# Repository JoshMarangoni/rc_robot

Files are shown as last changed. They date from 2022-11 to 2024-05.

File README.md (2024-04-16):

# rc_robot

## Project Motivation

NASA's Perseverance rover is a remote controllable rover designed to explore the surface of the Red Planet. The rover primarily uses an ultra-high frequency antenna to communicate with Earth. Data is relayed through Mars satellites back to Earth where engineers can monitor the robot's trajectory and speed.

Although my robot is not designed for Mars, it is designed to explore the outer reaches of my kitchen and living room while I am comfortably relaxing in my bedroom. Instead of orbitting satellites I use my WiFi network and communicate with my robot using http requests. This project is intended to emulate a remote controlled rover such as Perserverence, using my own circuit and software designs.

## Requirements

- Must be able to drive in any direction
- Programmed in C/C+
- Non-arduino based coding envrionment
- Battery powered
- Map "WASD" keys to driving direction

## Bonus features

- All electronics contained on one PCB
- Remote controlled using video feed
- Lag between key presses and robot response < 0.5 s

## Design 1 (MVP) - DONE

- ESP 32 microcontroller programmed in Arduino
- 2 wheels/motors in the rear (RWD)
- 1 wheel/motor in the front
- esp32CAM for video streaming
- Plexiglass chassis

## Design 2 (Feature Complete) - Done

- ESP32 programmed in Expressif IoT Development Framework
- PCB designed in KiCAD and fabricated by JLC PCB
- control terminal for WASD keys written in Python

### Planning (created after completing Design 1)
| Task | Deadline |
|---|---|
| get 3D printer working | Nov.19 (Sat) |
| receive MOSFETs | Nov.19 (Sat) |
| get H-bridges working | Nov.20 (Sun) |
| test singular power source with capacitor | Nov.20 (Sun) |
| finish PCB design and send order for fab | Nov.27 (Sun) |
| make CAD drawing for chassis and 3D print | Dec.4  (Sun) |
| receive PCB | Dec.7  (Wed) |
| solder components on PCB and test | Dec.11 (Sun) |
| finish all software | Dec.18 (Sun) |

### Demo YouTube Videos
H bridge Circuit Theory - 2 Wire Input Design (https://www.youtube.com/watch?v=d1yoUQiy7Vs)

Making an H Bridge PCB in KiCad from scratch! (https://www.youtube.com/watch?v=Di--UKmRp28)

Assembling and Testing ESP32 H Bridge PCB (https://www.youtube.com/watch?v=TdYsxLpm71Q)

Remote Control Robot with ChatGPT and Embedded Web Server on ESP32 (https://www.youtube.com/watch?v=ufaAewCI-w4)

### Key Learnings
- even though a motor draws 0.2 A while running it can produce a stall current of 2+ A, causing the driver to underpower the arduino
  - meaured the 5V output of the Arduino and saw the voltage hang around 3 V sometimes dropping even lower as the motors change directions. I need to either put the motors on a separate power supply or use large capacitors to buffer voltage spikes
  - After doing some research I found out that the larger the current draw is from the battery, the lower the batteries output voltage will be due to the internal voltage drop. Batteries have an internal resistance, so the larger the current out of the battery, the larger the internal drop, and the lower the output voltage will be. Hypothesis, to solve this, use batteries with larger capacity, such as two 18650's in series, which have a combined 2800mAh capacity. Results: it worked!
- Got video streaming over Bluetooth by changing ArduCAM's serial prints to use SerialBT, then using a BT virtual COM port for the host app
- Tried combining all the camera source code, bluetooth serial, http webserver, and motor controls all in one program, but the program is too large for the ESP32. Further, I do not want the camera streaming software to be delayed by running motor controls and http server responses in the same control loop. I could use FreeRTOS to split up these tasks, but that seems overkill. There is no need to have all this code on one processor when I can buy an integrated esp32-CAM that I can dedicate to video streaming. Having the robot be controlled over WIFI is also superior to Bluetooth as it allows me to operate the vehicle compleletely remotely as long as I have the WIFI router's IP address and port forwarding setup.
- Do a beep test on a PCB before placing components
- DO NOT POWER UP PCB UNTIL YOU ARE SURE EVERYTHING IS CONNECTED PROPERLY
- BE VERY SURE you don't mix up power and ground, as reversing the polarity will surely fry your components
- If hand soldering a PCB, do it in stages, and test each module individually as you go

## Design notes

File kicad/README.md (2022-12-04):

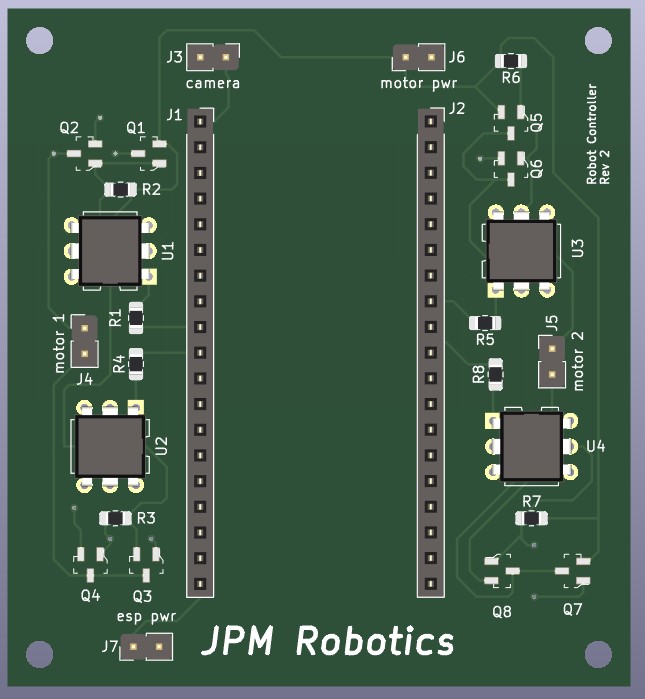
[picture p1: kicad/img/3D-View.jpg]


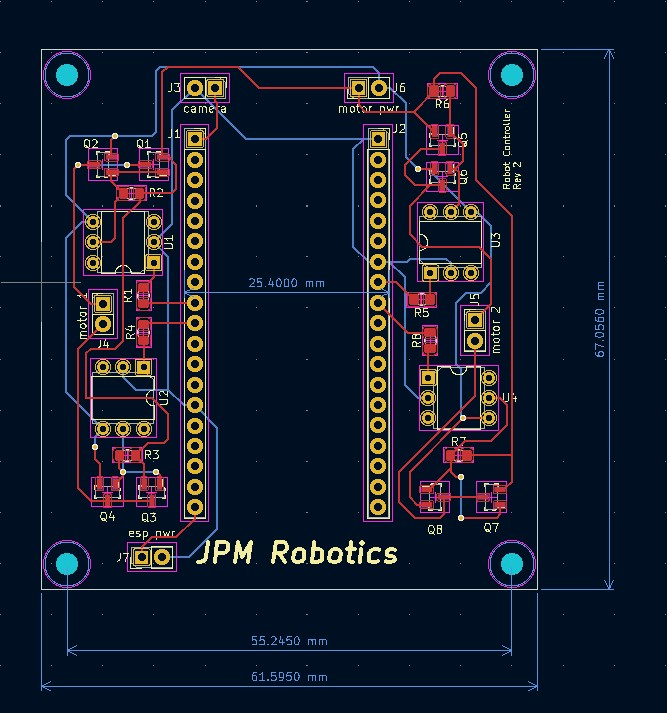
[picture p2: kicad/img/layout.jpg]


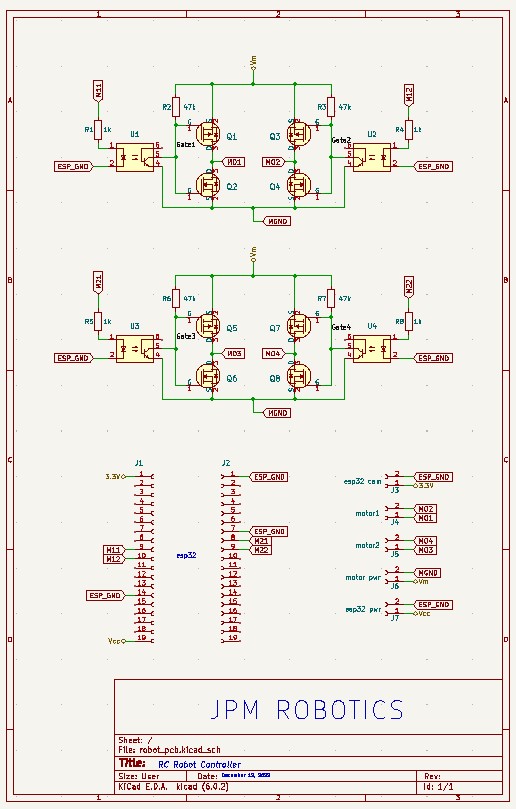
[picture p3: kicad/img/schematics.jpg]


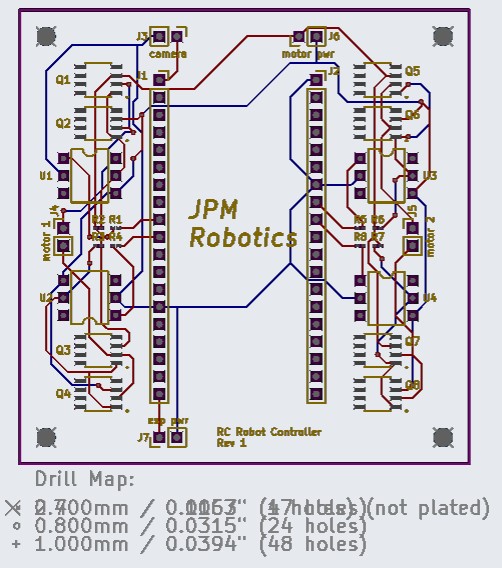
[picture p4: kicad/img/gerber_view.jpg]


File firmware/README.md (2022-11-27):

### Flash command Windows

C:\Users\joshu\Documents\ArduinoData\packages\esp32\tools\esptool_py\3.0.0/esptool.exe --chip esp32 --port COM6 --baud 921600 --before default_reset --after hard_reset write_flash -z --flash_mode dio --flash_freq 80m --flash_size detect 0xe000 C:\Users\joshu\Documents\ArduinoData\packages\esp32\hardware\esp32\1.0.6/tools/partitions/boot_app0.bin 0x1000 C:\Users\joshu\Documents\ArduinoData\packages\esp32\hardware\esp32\1.0.6/tools/sdk/bin/bootloader_qio_80m.bin 0x10000 C:\Users\joshu\AppData\Local\Temp\arduino_build_810982/sketch_nov27a.ino.bin 0x8000 C:\Users\joshu\AppData\Local\Temp\arduino_build_810982/sketch_nov27a.ino.partitions.bin

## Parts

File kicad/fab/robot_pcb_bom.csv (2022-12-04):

Comment | Designator | Package | Quantity | Designation | LCSC Part Number
2-pin male header | J7 | PinHeader_1x02_P2.54mm_Vertical | 1 | esp32 pwr
pmos transistor (30V,4A) | Q3,Q1,Q7,Q5 | SOT-23-3 | 4 | AO3401A | C15127
19-pin female header | J1,J2 | PinSocket_1x19_P2.54mm_Vertical | 2 | Conn_01x19_Female
nmos transistor (30V, 5A) | Q4,Q6,Q8,Q2 | SOT-23-3 | 4 | IRLML6344TRPBF | C53550
2-pin male header | J3 | PinHeader_1x02_P2.54mm_Vertical | 1 | esp32 cam
1k smd (0805) resistor | R5,R8,R1,R4 | R_0805_2012Metric_Pad1.20x1.40mm_HandSolder | 4 | 1k
optoisolater | U3,U1,U4,U2 | DIP-6_W7.62mm | 4 | 4N25 | C115480
47k smd (0805) resistor | R3,R6,R2,R7 | R_0805_2012Metric_Pad1.20x1.40mm_HandSolder | 4 | 47k
2-pin male header | J6 | PinHeader_1x02_P2.54mm_Vertical | 1 | motor pwr
2-pin male header | J4 | PinHeader_1x02_P2.54mm_Vertical | 1 | motor1
2-pin male header | J5 | PinHeader_1x02_P2.54mm_Vertical | 1 | motor2

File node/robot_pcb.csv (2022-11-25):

Comment | Designator | Footprint | Quantity | Part Number
2-pin male header | J7 | PinHeader_1x02_P2.54mm_Vertical | 1
pmos transistor | Q3,Q1,Q7,Q5 | SOIC127P490X600X175-8N | 4
19-pin female header | J1,J2 | PinSocket_1x19_P2.54mm_Vertical | 2
nmos transistor | Q4,Q6,Q8,Q2 | SOIC127P490X600X175-8N | 4
2-pin male header | J3 | PinHeader_1x02_P2.54mm_Vertical | 1
1k smd resistor | R5,R8,R1,R4 | R_0201_0603Metric_Pad0.64x0.40mm_HandSolder | 4
optoisolater | U3,U1,U4,U2 | DIP-6_W7.62mm | 4 | 4N25
47k smd resistor | R3,R6,R2,R7 | R_0201_0603Metric_Pad0.64x0.40mm_HandSolder | 4
2-pin male header | J6 | PinHeader_1x02_P2.54mm_Vertical | 1
2-pin male header | J4 | PinHeader_1x02_P2.54mm_Vertical | 1
2-pin male header | J5 | PinHeader_1x02_P2.54mm_Vertical | 1

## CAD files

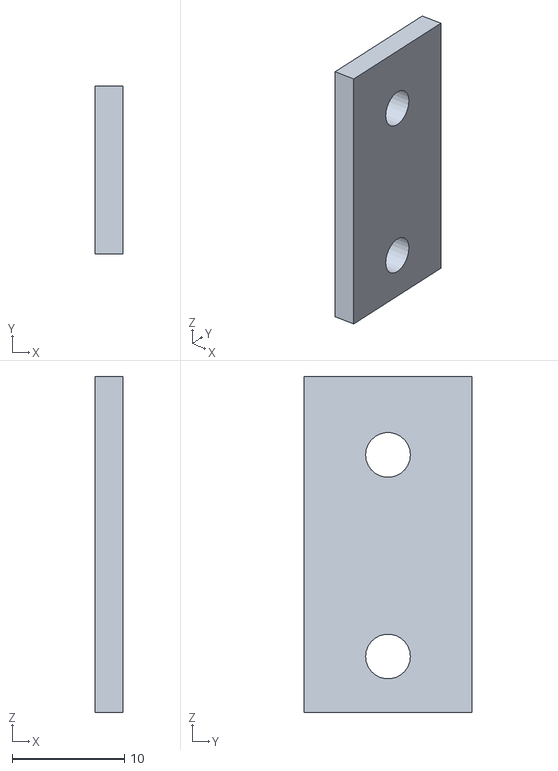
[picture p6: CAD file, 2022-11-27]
freecad/rc_robot-MotorHolder.stl
2.50 x 15.0 x 30.0

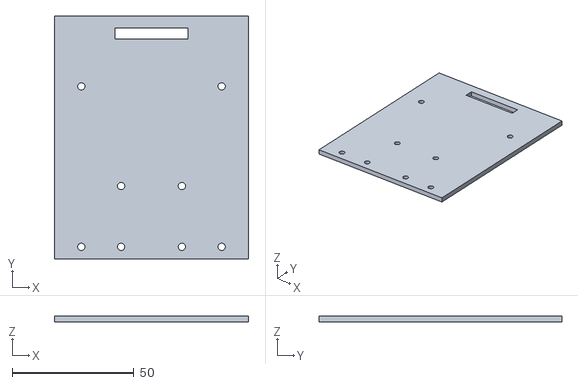
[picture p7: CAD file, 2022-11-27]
freecad/rc_robot-Base-stl.stl
80.0 x 100.0 x 2.50

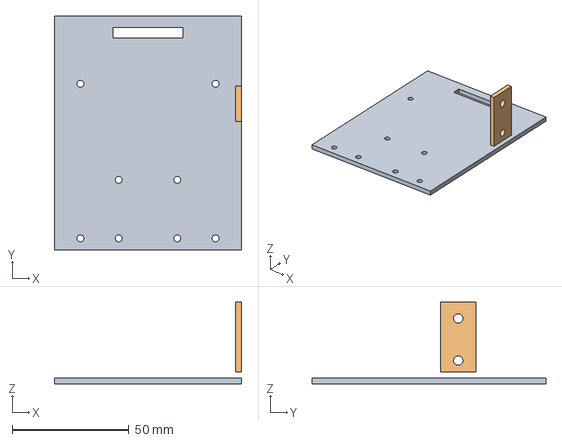
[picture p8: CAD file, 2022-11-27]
freecad/rc_robot.FCStd
80.0 x 100.0 x 35.0 mm
Base
MotorHolder

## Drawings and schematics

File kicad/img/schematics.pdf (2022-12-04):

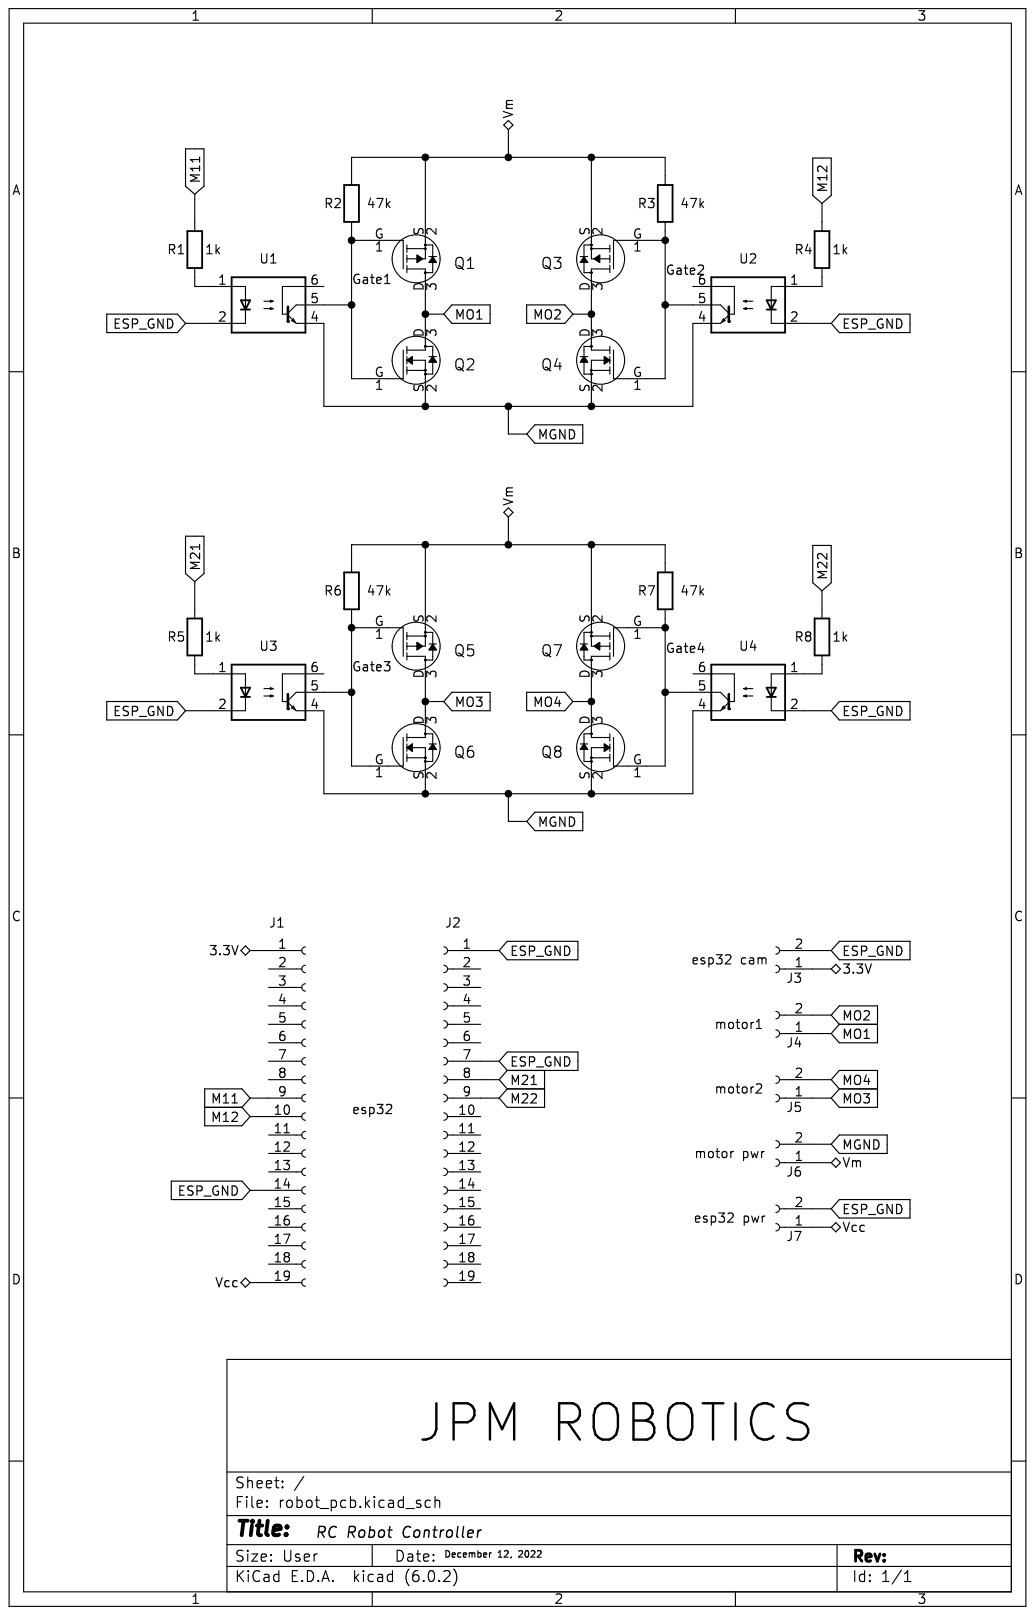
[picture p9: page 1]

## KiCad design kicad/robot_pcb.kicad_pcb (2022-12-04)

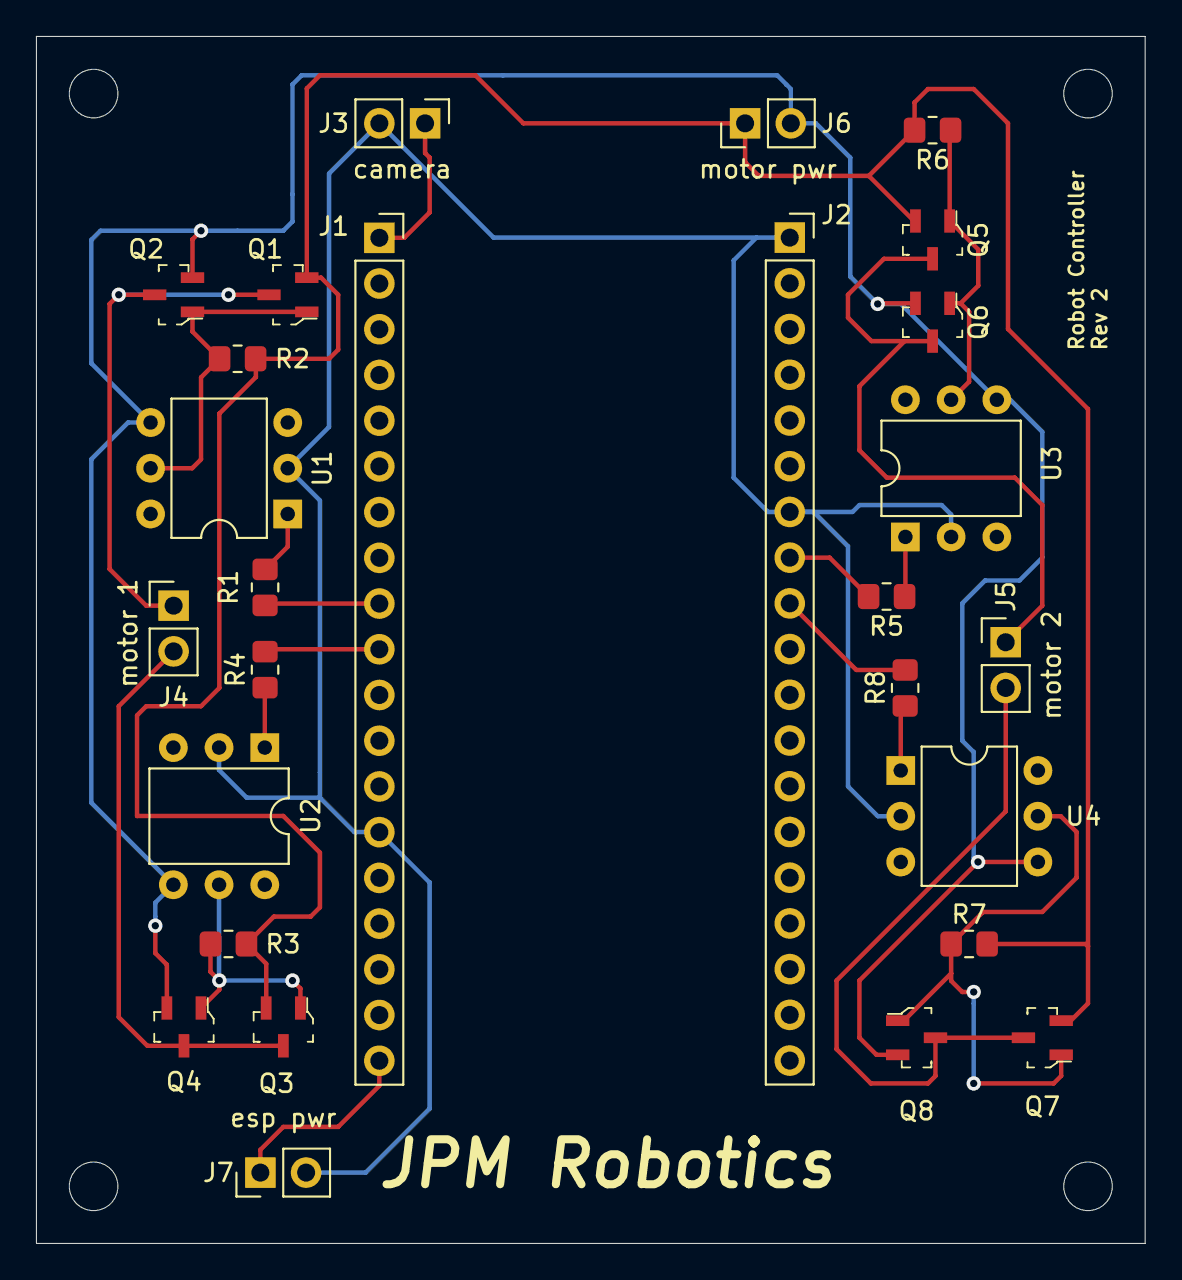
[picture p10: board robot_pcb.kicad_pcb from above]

Board: 2 copper layers, 61.6 x 67.1 mm, 31 parts (0 on the bottom side), 21 nets.

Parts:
J1, J2: Conn_01x19_Female; PinSocket_1x19_P2.54mm_Vertical
J3: esp32 cam; PinHeader_1x02_P2.54mm_Vertical
J4: motor1; PinHeader_1x02_P2.54mm_Vertical
J5: motor2; PinHeader_1x02_P2.54mm_Vertical
J6: motor pwr; PinHeader_1x02_P2.54mm_Vertical
J7: esp32 pwr; PinHeader_1x02_P2.54mm_Vertical
Q1, Q3, Q5, Q7: AO3401A; SOT-23-3
Q2, Q4, Q6, Q8: IRLML6344TRPBF; SOT-23-3
R1, R4, R5, R8: 1k; R_0805_2012Metric_Pad1.20x1.40mm_HandSolder
R2, R3, R6, R7: 47k; R_0805_2012Metric_Pad1.20x1.40mm_HandSolder
REF1, REF2, REF3, REF4: MountingHole_2.7mm_M2.5
U1, U2, U3, U4: 4N25; DIP-6_W7.62mm

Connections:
/3.3V: J1.1, J3.1
/Gate1: Q1.1 (G), Q2.1 (G), R2.1, U1.5
/Gate2: Q3.1 (G), Q4.1 (G), R3.1, U2.5
/Gate3: Q5.1 (G), Q6.1 (G), R6.1, U3.5
/Gate4: Q7.1 (G), Q8.1 (G), R7.1, U4.5
/Vcc: J1.19, J7.1
/Vm: J6.1, Q1.2 (S), Q3.2 (S), Q5.2 (S), Q7.2 (S), R2.2, R3.2, R6.2, R7.2
ESP_GND: J1.14, J2.1, J2.7, J3.2, J7.2, U1.2, U2.2, U3.2, U4.2
M11: J1.9, R1.2
M12: J1.10, R4.2
M21: J2.8, R5.2
M22: J2.9, R8.2
MGND: J6.2, Q2.2 (S), Q4.2 (S), Q6.2 (S), Q8.2 (S), U1.4, U2.4, U3.4, U4.4
MO1: J4.1, Q1.3 (D), Q2.3 (D)
MO2: J4.2, Q3.3 (D), Q4.3 (D)
MO3: J5.1, Q5.3 (D), Q6.3 (D)
MO4: J5.2, Q7.3 (D), Q8.3 (D)
unnamed: R1.1, U1.1
unnamed: R4.1, U2.1
unnamed: R5.1, U3.1
unnamed: R8.1, U4.1

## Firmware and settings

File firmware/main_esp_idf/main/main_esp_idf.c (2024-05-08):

#include <esp_event.h>
#include <esp_system.h>
#include <esp_wifi.h>
#include <stdio.h>
#include <sys/param.h>

#include "driver/gpio.h"
#include "esp_eth.h"
#include "esp_http_server.h"
#include "esp_log.h"
#include "esp_netif.h"
#include "esp_tls_crypto.h"
#include "freertos/FreeRTOS.h"
#include "freertos/task.h"
#include "nvs_flash.h"
#include "protocol_examples_common.h"
#include "sdkconfig.h"

#define  LED_PIN         2U
#define  MOTOR_PIN_M11   25U
#define  MOTOR_PIN_M12   26U
#define  MOTOR_PIN_M21   19U
#define  MOTOR_PIN_M22   18U
#define  HIGH            1U
#define  LOW             0U

static const char *TAG = "INFO";
static uint8_t s_led_state = 0;

static void blink_led(void)
{
    gpio_set_level(LED_PIN, s_led_state);
}

static void configure_led(void)
{
    gpio_reset_pin(LED_PIN);
    gpio_set_direction(LED_PIN, GPIO_MODE_OUTPUT);
    ESP_LOGI(TAG, "On board LED initialized");
}

static void configure_motor_pins(void)
{
    gpio_reset_pin(MOTOR_PIN_M11);
    gpio_set_direction(MOTOR_PIN_M11, GPIO_MODE_OUTPUT);

    gpio_reset_pin(MOTOR_PIN_M12);
    gpio_set_direction(MOTOR_PIN_M12, GPIO_MODE_OUTPUT);

    gpio_reset_pin(MOTOR_PIN_M21);
    gpio_set_direction(MOTOR_PIN_M21, GPIO_MODE_OUTPUT);

    gpio_reset_pin(MOTOR_PIN_M22);
    gpio_set_direction(MOTOR_PIN_M22, GPIO_MODE_OUTPUT);

    ESP_LOGI(TAG, "Motors initialized");
}

static void drive_straight()
{
    ESP_LOGI(TAG, "Going straight");
    gpio_set_level(MOTOR_PIN_M11, LOW);
    gpio_set_level(MOTOR_PIN_M12, HIGH);
    gpio_set_level(MOTOR_PIN_M21, LOW);
    gpio_set_level(MOTOR_PIN_M22, HIGH);
}

static void turn_left()
{
    ESP_LOGI(TAG, "Turning left");
    gpio_set_level(MOTOR_PIN_M11, LOW);
    gpio_set_level(MOTOR_PIN_M12, LOW);
    gpio_set_level(MOTOR_PIN_M21, LOW);
    gpio_set_level(MOTOR_PIN_M22, HIGH);
}

static void drive_backwards()
{
    ESP_LOGI(TAG, "Going backwards");
    gpio_set_level(MOTOR_PIN_M11, HIGH);
    gpio_set_level(MOTOR_PIN_M12, LOW);
    gpio_set_level(MOTOR_PIN_M21, HIGH);
    gpio_set_level(MOTOR_PIN_M22, LOW);
}

static void turn_right()
{
    ESP_LOGI(TAG, "Turning right");
    gpio_set_level(MOTOR_PIN_M11, LOW);
    gpio_set_level(MOTOR_PIN_M12, HIGH);
    gpio_set_level(MOTOR_PIN_M21, LOW);
    gpio_set_level(MOTOR_PIN_M22, LOW);
}

static void stop()
{
    ESP_LOGI(TAG, "Stopping");
    gpio_set_level(MOTOR_PIN_M11, LOW);
    gpio_set_level(MOTOR_PIN_M12, LOW);
    gpio_set_level(MOTOR_PIN_M21, LOW);
    gpio_set_level(MOTOR_PIN_M22, LOW);
}

static esp_err_t get_handler(httpd_req_t *req)
{
    esp_err_t ret;
    char* response_data = req->user_ctx;
    char* response_code = "200";

    if (strcmp(req->uri, "/blink") == 0)
    {
        s_led_state = !s_led_state;
        blink_led();
    }
    else if (strcmp(req->uri, "/drive/w") == 0)
    {
        drive_straight();
    }
    else if (strcmp(req->uri, "/drive/a") == 0)
    {
        turn_left();
    }
    else if (strcmp(req->uri, "/drive/s") == 0)
    {
        drive_backwards();
    }
    else if (strcmp(req->uri, "/drive/d") == 0)
    {
        turn_right();
    }
    else if (strcmp(req->uri, "/drive/q") == 0)
    {
        stop();
    }
    else
    {
        response_data = "Unknown Request";
        response_code = "404";  // Not found status code
    }

    // Note: client should be setup to not rely on a response,
    // but it is helpful to have a response nonetheless.
    httpd_resp_set_status(req, response_code);
    ret = httpd_resp_send(req, response_data, HTTPD_RESP_USE_STRLEN);
    if (ret != ESP_OK)
    {
        ESP_LOGE("HTTPD", "Failed to send response: %s", esp_err_to_name(ret));
    }

    return ret;
}

static const httpd_uri_t hello = {
    .uri       = "/hello",
    .method    = HTTP_GET,
    .handler   = get_handler,
    .user_ctx  = "Hello World!"
};

static const httpd_uri_t blink = {
    .uri       = "/blink",
    .method    = HTTP_GET,
    .handler   = get_handler,
    .user_ctx  = "LED TOGGLED"
};

static const httpd_uri_t drive_w = {
    .uri       = "/drive/w",
    .method    = HTTP_GET,
    .handler   = get_handler,
    .user_ctx  = "DRIVING STRAIGHT"
};

static const httpd_uri_t drive_a = {
    .uri       = "/drive/a",
    .method    = HTTP_GET,
    .handler   = get_handler,
    .user_ctx  = "TURNING LEFT"
};

static const httpd_uri_t drive_s = {
    .uri       = "/drive/s",
    .method    = HTTP_GET,
    .handler   = get_handler,
    .user_ctx  = "DRIVING BACKWARDS"
};

static const httpd_uri_t drive_d = {
    .uri       = "/drive/d",
    .method    = HTTP_GET,
    .handler   = get_handler,
    .user_ctx  = "TURNING RIGHT"
};

static const httpd_uri_t drive_q = {
    .uri       = "/drive/q",
    .method    = HTTP_GET,
    .handler   = get_handler,
    .user_ctx  = "STOPPING"
};

httpd_handle_t start_webserver(void)
{
    httpd_config_t config = HTTPD_DEFAULT_CONFIG();
    httpd_handle_t server = NULL;

    ESP_LOGI(TAG, "Starting server on port: '%d'", config.server_port);
    bool serverStarted = httpd_start(&server, &config) == ESP_OK;

    if (serverStarted)
    {
        httpd_register_uri_handler(server, &hello);
        httpd_register_uri_handler(server, &blink);
        httpd_register_uri_handler(server, &drive_w);
        httpd_register_uri_handler(server, &drive_a);
        httpd_register_uri_handler(server, &drive_s);
        httpd_register_uri_handler(server, &drive_d);
        httpd_register_uri_handler(server, &drive_q);
    }
    else
    {
        ESP_LOGI(TAG, "Error starting server!");
    }

    return server;
}

static esp_err_t stop_webserver(httpd_handle_t server)
{
    return httpd_stop(server);
}

static void disconnect_handler(void* arg,
                               esp_event_base_t event_base,
                               int32_t event_id,
                               void* event_data)
{
    httpd_handle_t* server = (httpd_handle_t*) arg;
    if (*server) {
        ESP_LOGI(TAG, "Stopping webserver");
        if (stop_webserver(*server) == ESP_OK) {
            *server = NULL;
        } else {
            ESP_LOGE(TAG, "Failed to stop http server");
        }
    }
}

static void connect_handler(void* arg,
                            esp_event_base_t event_base,
                            int32_t event_id,
                            void* event_data)
{
    httpd_handle_t* server = (httpd_handle_t*) arg;
    if (*server == NULL) {
        ESP_LOGI(TAG, "Starting webserver");
        *server = start_webserver();
    }
}

void app_main(void)
{
    ESP_LOGI(TAG, "APP BEGIN");

    configure_led();
    configure_motor_pins();

    static httpd_handle_t server = NULL;

    ESP_ERROR_CHECK(nvs_flash_init());  // Initialize and verify Non-Volatile Storage
    ESP_ERROR_CHECK(esp_netif_init());  // Initialize and verify network interfaces
    ESP_ERROR_CHECK(esp_event_loop_create_default());  // Sets up the default system event loop

    ESP_ERROR_CHECK(example_connect()); // Configure WiFi
    ESP_ERROR_CHECK(esp_event_handler_register(IP_EVENT, IP_EVENT_STA_GOT_IP, &connect_handler, &server)); // received IP "event"
    ESP_ERROR_CHECK(esp_event_handler_register(WIFI_EVENT, WIFI_EVENT_STA_DISCONNECTED, &disconnect_handler, &server));

    server = start_webserver();
}

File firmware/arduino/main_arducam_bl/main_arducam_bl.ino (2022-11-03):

#include "BluetoothSerial.h"

#if !defined(CONFIG_BT_ENABLED) || !defined(CONFIG_BLUEDROID_ENABLED)
#error Bluetooth is not enabled! Please run `make menuconfig` to and enable it
#endif

BluetoothSerial SerialBT;

#include <WiFi.h>

#define IN1 18
#define IN2 19
#define IN3 22
#define IN4 23
#define LED 32

String Drive_State = "off";

const char* ssid = "";
const char* password = "";

WiFiServer server(80);

String header;

// Auxiliar variables to store the current output state
String LED_State = "off";

// Current time
unsigned long currentTime = millis();

// Previous time
unsigned long previousTime = 0;

// Define timeout time in milliseconds (example: 2000ms = 2s)
const long timeoutTime = 2000;

void straight() {
    digitalWrite(IN1, HIGH);
    digitalWrite(IN2, LOW);
    digitalWrite(IN4, HIGH);
    digitalWrite(IN3, LOW);
}

void left() {
    digitalWrite(IN1, HIGH);
    digitalWrite(IN2, LOW);
    digitalWrite(IN4, LOW);
    digitalWrite(IN3, HIGH);
}

void right() {
    digitalWrite(IN1, LOW);
    digitalWrite(IN2, HIGH);
    digitalWrite(IN4, HIGH);
    digitalWrite(IN3, LOW);
}

void off() {
    digitalWrite(IN1, LOW);
    digitalWrite(IN2, LOW);
    digitalWrite(IN4, LOW);
    digitalWrite(IN3, LOW);
}

#include <Wire.h>
#include <ArduCAM.h>
#include <SPI.h>
#include "memorysaver.h"

//This demo can only work on OV2640_MINI_2MP or OV5642_MINI_5MP or OV5642_MINI_5MP_BIT_ROTATION_FIXED platform.
#if !( defined OV2640_MINI_2MP_PLUS)
#error Please select the hardware platform and camera module in the ../libraries/ArduCAM/memorysaver.h file
#endif

#define BMPIMAGEOFFSET 66

const char bmp_header[BMPIMAGEOFFSET] PROGMEM =
{
    0x42, 0x4D, 0x36, 0x58, 0x02, 0x00, 0x00, 0x00, 0x00, 0x00, 0x42, 0x00, 0x00, 0x00, 0x28, 0x00,
    0x00, 0x00, 0x40, 0x01, 0x00, 0x00, 0xF0, 0x00, 0x00, 0x00, 0x01, 0x00, 0x10, 0x00, 0x03, 0x00,
    0x00, 0x00, 0x00, 0x58, 0x02, 0x00, 0xC4, 0x0E, 0x00, 0x00, 0xC4, 0x0E, 0x00, 0x00, 0x00, 0x00,
    0x00, 0x00, 0x00, 0x00, 0x00, 0x00, 0x00, 0xF8, 0x00, 0x00, 0xE0, 0x07, 0x00, 0x00, 0x1F, 0x00,
    0x00, 0x00
};

const int CS = 5; // slave select pin
bool is_header = false;
int mode = 0;
uint8_t start_capture = 0;

ArduCAM myCAM( OV2640, CS );

uint8_t read_fifo_burst(ArduCAM myCAM);

void setup() {
    uint8_t vid, pid, temp;
    Wire.begin();
    Serial.begin(115200);

    SerialBT.println(F("ACK CMD ArduCAM Start! END"));
    SerialBT.begin("ESP32test"); //Bluetooth device name
    SerialBT.println("Initialization Successful.");
    SerialBT.println("The device started, now you can pair it with bluetooth!");

    // set the CS as an output:
    pinMode(CS, OUTPUT);
    digitalWrite(CS, HIGH);

    // initialize SPI:
    SPI.begin();

    //Reset the CPLD
    myCAM.write_reg(0x07, 0x80);
    delay(100);
    myCAM.write_reg(0x07, 0x00);
    delay(100);

    while (1)
    {
        //Check if the ArduCAM SPI bus is OK
        myCAM.write_reg(ARDUCHIP_TEST1, 0x55);
        temp = myCAM.read_reg(ARDUCHIP_TEST1);
        if (temp != 0x55)
        {
            SerialBT.println(F("ACK CMD SPI interface Error!END"));
            delay(1000);
            continue;
        }
        else
        {
            SerialBT.println(F("ACK CMD SPI interface OK.END"));
            break;
        }
    }

    while (1)
    {
        //Check if the camera module type is OV2640
        myCAM.wrSensorReg8_8(0xff, 0x01);
        myCAM.rdSensorReg8_8(OV2640_CHIPID_HIGH, &vid);
        myCAM.rdSensorReg8_8(OV2640_CHIPID_LOW, &pid);
        if ((vid != 0x26 ) && (( pid != 0x41 ) || ( pid != 0x42 )))
        {
            SerialBT.println(F("ACK CMD Can't find OV2640 module!"));
            delay(1000); continue;
        }
        else
        {
            SerialBT.println(F("ACK CMD OV2640 detected.END")); break;
        }
    }
    //Change to JPEG capture mode and initialize the OV5642 module
    myCAM.set_format(JPEG);
    myCAM.InitCAM();
    myCAM.OV2640_set_JPEG_size(OV2640_320x240);
    delay(1000);
    myCAM.clear_fifo_flag();

    // motors
    pinMode(IN1, OUTPUT);
    pinMode(IN2, OUTPUT);
    pinMode(IN3, OUTPUT);
    pinMode(IN4, OUTPUT);
    off();
    Serial.println("Motor Driver Initialized");

    // webserver
    pinMode(LED, OUTPUT);
    digitalWrite(LED, HIGH);
    // Connect to Wi-Fi network with SSID and password
    Serial.print("Connecting to ");
    Serial.println(ssid);
    WiFi.begin(ssid, password);

    while (WiFi.status() != WL_CONNECTED) {
        delay(500);
        Serial.print(".");
    }

    // Print local IP address and start web server
    Serial.println("");
    Serial.println("WiFi connected.");
    Serial.println("IP address: ");
    Serial.println(WiFi.localIP());
    server.begin();
}
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

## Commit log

2022-09-06 basic motor control
2022-09-10 update motor driver
2022-09-11 motor drive with esp32
2022-09-11 add HTTP LED control
2022-09-12 http motor control
2022-10-12 print serial over Bluetooth
2022-11-02 add motor and web server code
2022-11-07 upload esp32 cam code
2022-11-16 copy node pcb project
    [node-B_Cu.gbr, node-B_Mask.gbr, node-B_Paste.gbr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]
2022-11-16 make robot schematics
    [node.kicad_sch, robot.kicad_sch]
2022-11-16 add node for reference
    [node.kicad_sch, robot.kicad_pcb, robot.kicad_sch]
2022-11-19 single power source working!
2022-11-21 h-bridge motor test
2022-11-22 pcb layout
    [robot_pcb.kicad_pcb, robot_pcb.kicad_sch]
2022-11-25 pcb design complete
    [robot_pcb.kicad_pcb, robot_pcb.kicad_sch]
2022-11-25 pcb done
    [robot_pcb-B_Cu.gbl, robot_pcb-B_Mask.gbs, robot_pcb-B_Paste.gbp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]
2022-11-25 generate gerbers
    [robot_pcb-B_Cu.gbl, robot_pcb-B_Mask.gbs, robot_pcb-B_Paste.gbp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]
2022-11-26 create chassis CAD
    [rc_robot-Base.stl, rc_robot-MotorAHolder1.stl, rc_robot.FCStd]
2022-11-26 add measurements kicad
    [robot_pcb.kicad_pcb]
2022-11-27 update stl
    [rc_robot-Base-stl.stl, rc_robot-Base.stl, rc_robot-MotorAHolder1.stl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]
2022-11-27 move sketches to arduino folder
2022-11-27 upload arduino folder
2022-11-27 upload first kicad image
2022-11-27 create sample main esp idf
2022-11-27 blink LED
2022-11-28 add LED toggle to http server
2022-11-28 add function stubs for motor controls
2022-11-28 implement motor drivers
2022-12-04 pcb rev 2
    [robot_pcb.kicad_pcb, robot_pcb.kicad_sch]
2022-12-04 exclude kicad backups
2022-12-04 sent out fab for rev2 pcb
    [robot_pcb-B_Cu.gbl, robot_pcb-B_Mask.gbs, robot_pcb-B_Paste.gbp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]
2022-12-04 add measurements
    [robot_pcb.kicad_pcb]
2023-05-14 arduino control test both motors
2023-05-16 update motor pins
2024-05-01 update motor controls
